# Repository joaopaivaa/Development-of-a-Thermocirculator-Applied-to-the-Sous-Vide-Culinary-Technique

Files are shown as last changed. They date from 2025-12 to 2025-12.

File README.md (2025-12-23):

## Development of a Thermocirculator Applied to the Sous Vide Culinary Technique

Paper in english published on "Revista Cereus" from Brazil (https://www.ojs.unirg.edu.br/index.php/1/article/view/5994)

Developed in 2019-2023 in collaboration with Erinaldo Nascimento, MSc and Camila Miranda, PhD as part of my electrical engineering BSc final paper and undergraduate research.

Abstract:
This paper addresses the theory, design, and execution of a thermocirculator, developing its electronic circuits, printed circuit boards (PCBs), plastic structure, and equipment assembling. The developed thermocirculator is based on 3 previous prototypes, with the first one being created in 2019. The ESP32 microcontroller was used as the basis for the electronic circuits. MicroPython was chosen as the programming language, and a web server was developed to connect the user and the equipment via Wi-Fi, allowing monitoring of the equipment from anywhere. An On-Off controller was implemented to keep the water temperature constant. The plastic structure was made of ABS plastic, and manufactured by 3D printing, with lateral dimensions of 7 x 7 cm and 18.5 cm of height, divided into upper portion, medial cover, lower portion, and lower covers. After the equipment was assembled, tests were made to verify its operation, which consisted of preparing foods such as a NY strip steak at 55 ºC, pork ribs at 70 ºC, and eggs at different temperatures. The developed thermocirculator performs its function excellently and can prepare food like a commercial product, fulfilling the objectives established by this paper.

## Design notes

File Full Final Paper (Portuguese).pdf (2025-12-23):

UNIVERSIDADE ESTADUAL DE MARINGÁ

DEPARTAMENTO DE ENGENHARIA QUÍMICA

CURSO DE ENGENHARIA ELÉTRICA

JOÃO VITOR DE PAIVA MARCOTTI

DESENVOLVIMENTO DE UM TERMOCIRCULADOR APLICADO À TÉCNICA CULINÁRIA SOUS VIDE

TRABALHO DE CONCLUSÃO DE CURSO

MARINGÁ

2023

JOÃO VITOR DE PAIVA MARCOTTI

DESENVOLVIMENTO DE UM TERMOCIRCULADOR APLICADO À TÉCNICA CULINÁRIA SOUS VIDE

Trabalho | de | Conclusão | de | Curso
apresentado | ao | Departamento | de
Engenharia Química, curso de Engenharia Elétrica da Universidade Estadual de
Maringá, | como | requisito | parcial à
obtenção | do | título de Engenheiro
Eletricista.

Orientador: Prof. Dr. Camila de Brito Miranda
Coorientador: Prof. Me. Erinaldo Sanches Nascimento

MARINGÁ

2023

- O Termo de Aprovação assinado encontra-se na Coordenação do Curso -

Dedico este trabalho à minha família e amigos, em especial à minha mãe, Patrícia Fernandes de Paiva, por todo o apoio e incentivo durante estes 5 anos de graduação.

AGRADECIMENTOS

Certamente estes parágrafos não irão atender a todas as pessoas que fizeram parte desta importante e única fase de minha vida, a graduação. Desta forma, devo citar os maiores responsáveis por todo o meu avanço ao longo destes 5 anos.
Primeiramente, agradeço à minha família por todo o incentivo aos estudos e apoio durante os bons e maus momentos deste período.
Agradeço à minha namorada por todo o apoio ao longo da realização deste trabalho, sendo, sem dúvidas, meu maior suporte emocional nos momentos de incerteza e insegurança.
Sou grato à minha orientadora Profa. Dra. Camila de Brito Miranda Faia, por todo o tempo, auxílio, preocupação e dedicação durante o desenvolvimento deste projeto.
Agradeço ao meu co-orientador Prof. Me. Erinaldo Sanches Nascimento, por toda a sua parceria e dedicação a este projeto que se iniciou como uma iniciação científica e se estendeu a este trabalho.
Aos meus colegas de vida e de sala de aula Felipe Gerber, Gabriel Dias, Gabriel Scapim e Kenzo Kayzuka, agradeço por toda a parceria durante os estudos, trabalhos e provas da faculdade, em especial durante a pandemia de Covid-19. Sempre juntos e apoiando uns aos outros nos bons e maus momentos. Sem vocês nada disso seria possível.
Devo mencionar também meu maior ídolo na gastronomia e por meio de quem conheci a técnica culinária Sous Vide, tema deste trabalho, Gustavo Tosta, mais conhecido como Guga Foods.
Agradeço meu pai, por todo o incentivo aos estudos e ao trabalho. Agradeço individualmente minha irmã, com quem divido a mesma moradia há 6 anos, e me apoia em minhas escolhas desde o ensino médio.
Por fim, enfatizo um agradecimento especial a quem me deu a vida e foi a única pessoa que nunca duvidou de mim, da minha capacidade, das minhas ideias e dos meus objetivos, e sempre foi o meu maior apoio, minha mãe Patricia Fernandes de Paiva.

Ideias, e somente ideias, podem iluminar a escuridão. (VON MISES, Ludwig)

RESUMO

MARCOTTI, João Vitor de Paiva. Desenvolvimento de um termocirculador aplicado à técnica culinária Sous Vide. 2023. 46 f. Trabalho de Conclusão de Curso (Bacharelado em Engenharia Elétrica) - Universidade Estadual de Maringá. Maringá, 2023.

Este trabalho aborda a teoria, o projeto e a execução de um termocirculador aplicado à técnica culinária Sous Vide, desenvolvendo seus circuitos eletrônicos, placas de circuito impresso (na sigla em inglês PCB - Printed Circuit Board), estrutura plástica, e até mesmo o planejamento de uma empresa fictícia responsável por desenvolver, fabricar, vender e distribuir termocirculadores. O termocirculador desenvolvido parte de 3 protótipos anteriores, sendo o primeiro elaborado em meados de 2019. O último, elaborado por Marcotti e Nascimento (2021), teve seu funcionamento impossibilitado em razão da grande quantidade de cabos conectores presentes em seu interior, o que impediu sua montagem. Desta forma, este projeto possui entre seus objetivos, a solução desta falha com a redução do número de cabos conectores, permitindo o funcionamento do equipamento. Como base para os circuitos eletrônicos desenvolvidos, utilizou-se o microcontrolador ESP32, que permite conexão Wi-Fi e Bluetooth entre usuário e equipamento. Para programar tal componente, utilizou-se a linguagem de programação MicroPython, e um servidor web foi desenvolvido a fim de conectar usuário e equipamento via Wi-Fi, permitindo o monitoramento deste de qualquer local com conexão à internet. Um controlador On-Off foi implementado com o objetivo de manter a temperatura da água constante durante o funcionamento do termocirculador. A estrutura plástica foi elaborada em plástico ABS, e fabricada via impressão 3D, possuindo como dimensões laterais 7 x 7 cm e altura de 18,5 cm, e é dividida em parte superior, tampa medial, parte inferior e tampas inferiores. Ainda, ímãs de neodímio localizados entre as tampas inferiores permitem que o termocirculador se fixe a um recipiente metálico. Após a montagem do equipamento, testes foram realizados com o objetivo de averiguar o funcionamento do termocirculador desenvolvido. Tais testes consistiram no preparo de alimentos, sendo eles bife de chorizo bovino a 55 ºC, costelinha suína a 70 ºC e ovos a diferentes temperaturas. A empresa fictícia foi nomeada como Termo 3D, em referência à fabricação da estrutura do equipamento, e seu planejamento foi elaborado contendo plano de negócios, modelo de negócios, marca e conclusão a respeito da viabilidade do negócio. A realização deste trabalho possibilitou colocar em prática diversos conhecimentos adquiridos em sala de aula, tais como o projeto de circuitos eletrônicos e de PCBs, além da análise e interpretação de datasheets de componentes. Por fim, pode-se afirmar que o termocirculador desenvolvido cumpre sua função com excelência, sendo capaz de preparar alimentos como um termocirculador comercializado no mercado, cumprindo os objetivos estabelecidos neste trabalho.

Palavras-chave: Controlador On-Off. Eletrônica. ESP32. Impressão 3D. MicroPython.

ABSTRACT

MARCOTTI, João Vitor de Paiva. Development of a thermocirculator applied to the Sous Vide culinary technique. 2023. 46 f. Trabalho de Conclusão de Curso (Bacharelado em Engenharia Elétrica) – Maringá State University - Paraná. Maringá, 2023.

This paper addresses the theory, design, and execution of a thermocirculator applied to the Sous Vide cooking technique, developing its electronic circuits, printed circuit boards (PCBs), plastic structure, and even the planning of a fictional company responsible for developing, manufacturing, selling, and distributing thermocirculators. The developed thermocirculator is based on 3 previous prototypes, with the first one being created in mid-2019. The last one, developed by Marcotti and Nascimento (2021), had its operation made impossible due to the large number of connector cables present inside, which prevented its assembly. Thus, one of the objectives of this project is to solve this flaw by reducing the number of connector cables, allowing the equipment to function. The ESP32 microcontroller was used as the basis for the developed electronic circuits, which allows Wi-Fi and Bluetooth connection between the user and the equipment. MicroPython programming language was used to program this component, and a web server was developed to connect the user and the equipment via Wi-Fi, allowing the monitoring of the equipment from anywhere with a connection. An On-Off controller was implemented to maintain the water temperature constant during the operation of the thermocirculator. The plastic structure was made of ABS plastic, and manufactured via 3D printing, with lateral dimensions of 7 x 7 cm and a height of 18.5 cm, divided into upper portion, medial cover, lower portion, and lower covers. Moreover, neodymium magnets located between the lower covers allow the thermocirculator to be fixed to a metallic container. After the equipment was assembled, tests were carried out to verify the operation of the developed thermocirculator, which consisted of preparing food such as NY strip steak at 55 ºC, pork ribs at 70 ºC, and eggs at different temperatures. The fictional company was named Termo 3D, referring to the manufacturing of the equipment's structure, and its planning included a business plan, a business model, a brand, and a conclusion regarding the business's viability. The accomplishment of this work made it possible to put into practice various knowledge acquired in the classroom, such as the design of electronic circuits and PCBs, as well as the analysis and interpretation of component datasheets. Finally, it can be said that the developed thermocirculator performs its function excellently, capable of preparing food like a thermocirculator marketed in the market, fulfilling the objectives established in this paper.

Keywords: 3D printing. Electronics. ESP32. Micropython. On-Off Controller.

LISTA DE ILUSTRAÇÕES

Figura 1 - Aplicação da técnica culinária Sous Vide. | 1
Figura 2 - Cocção por meio da técnica culinária Sous Vide. | 2
Figura 3 - Cocção por meio de técnica culinária tradicional (grelha à alta
temperatura). | 2
Figura 4 - Water oven Cetro Constantine. | 5
Figura 5 - Termocirculador Cetro SV95. | 6
Figura 6 - Microcontrolador ESP32-WROOM-32. | 8
Figura 7 - Conexões com o microcontrolador ESP32. | 13
Figura 8 - Ponte USB para UART. | 14
Figura 9 - Conexão do microcontrolador com um buzzer ativo. | 14
Figura 10 - Conexão entre microcontrolador e circuito de controle em tensão
alternada. | 15
Figura 11 - Conexão entre microcontrolador e display OLED. | 15
Figura 12 - Circuito divisor de tensão para coleta da variação de resistência de
um termistor. | 15
Figura 13 - LED indicador de alimentação. | 16
Figura 14 - Circuitos de pull up conectados ao microcontrolador. | 16
Figura 15 - Circuito de controle do motor CC (esquerda) e circuito de controle da
ventoinha (direita). | 17

Figura 16 - Conexão do microcontrolador com o sensor de nível d’água
(esquerda) e com o sensor de temperatura em sonda (direita). | 17
Figura 17 - Esquemático do circuito de alimentação. | 18
Figura 18 - Conversor AC-DC utilizado. | 18
Figura 19 - Regulador de tensão fixo LM1117-3.3. | 18
Figura 20 - Esquemático do circuito de controle em tensão alternada. | 19
Figura 21 - Placa de controle e alimentação. | 20
Figura 22 - Placa principal. | 20

Figura 23 - Disposição em torre das duas placas no interior do termocirculador. | 21
Figura 24 - Parte superior em vista isométrica. | 22
Figura 25 - Tampa medial em vista isométrica. | 23
Figura 26 - Parte inferior em vista isométrica. | 23
Figura 27 - Tampa inferior em vista isométrica. | 24
Figura 28 - Tampa inferior (imãs) em vista isométrica. | 24
Figura 29 - Vista isométrica da estrutura completa do termocirculador. | 25
Figura 30 - Fluxograma 1: Funcionamento da Etapa de Conexão Wi-Fi. | 30
Figura 31 - Fluxograma 2: Funcionamento do modo de espera do algoritmo de
programação desenvolvido. | 31

Figura 32 - Fluxograma 3: Funcionamento do modo de alerta do algoritmo de
programação desenvolvido. | 32

Figura 33 - Fluxograma 4: Funcionamento da primeira etapa do modo de
operação do algoritmo de programação desenvolvido. | 33

Figura 34 - Fluxograma 5: Funcionamento da segunda etapa do modo de
operação do algoritmo de programação desenvolvido. | 34

Figura 35 - Fluxograma 6: Funcionamento da terceira etapa do modo de
operação do algoritmo de programação desenvolvido. | 35

Figura 36 - Botão responsável por colocar o microcontrolador em modo de
download quando pressionado (KEY4). | 38

Figura 37 - Resistor (R1) e capacitor (C4) retirados da PCB após serem
destruídos em teste. | 39
Figura 38 - Página exibida pelo ponto de acesso para escolha da rede Wi-Fi. | 41
Figura 39 - Servidor web 1. | 42
Figura 40 - Servidor web 2. | 42
Figura 41 - Servidor web 3. | 42
Figura 42 - Modelo de Negócios Canvas elaborado. | 49
Figura 43 - Matriz SWOT. | 63
Figura 44 - Logo da empresa fictícia. | 64

Fotografia 1 - Periféricos presentes no termocirculador. | 11
Fotografia 2 - Faces da placa de controle e alimentação. | 25
Fotografia 3 - Faces da placa principal. | 26
Fotografia 4 - Foto da parte superior. | 26
Fotografia 5 - Foto da hélice. | 26
Fotografia 6 - Foto da parte inferior. | 27
Fotografia 7 - Foto da tampa medial. | 27
Fotografia 8 - Foto das duas partes da tampa de baixo. | 27
Fotografia 9 - Parafusos e porcas utilizados na montagem do termocirculador. | 28
Fotografia 10 - Termocirculador montado e completo. | 28
Fotografia 11 - Marca de incineração deixada na placa de controle e
alimentação. | 39
Fotografia 12 - Medição da diferença de potencial entre a panela e a bancada. | 40
Fotografia 13 - Medição da diferença de potencial entre a panela e a bancada
após a adição do fio de terra. | 40
Fotografia 14 - Termocirculador com temperatura desejada de 60 ºC. | 43
Fotografia 15 - Bife de chorizo preparado ao ponto menos (55 ºC). | 44
Fotografia 16 - Ovos cozidos a diferentes temperaturas (com casca). | 44

Fotografia 17 - Ovos cozidos a diferentes temperaturas (prontos para consumo). 45

Fotografia 18 - Costelinha suína preparada durante 4 horas. | 46
Gráfico 1 - Variação da temperatura da água pelo tempo. | 36
Gráfico 2 - Zoom da variação da temperatura da água pelo tempo. | 36
Gráfico 3 - Resistência do termistor em função da temperatura ambiente. | 37
Gráfico 4 - Taxa de sobrevivência de empresas em 2 anos de operação de
acordo com seu ano de fundação. | 48
Gráfico 5 - Faixa etária. | 52
Gráfico 6 - Renda em milhares de dólares. | 52

Gráfico 7 - Continente de residência. | 53
Gráfico 8 - Alimento mais preparado com o equipamento. | 53
Gráfico 9 - Maior atrativo para a compra do equipamento. | 53
Gráfico 10 - Valor máximo que pagaria em um termocirculador. | 54
Gráfico 11 - Fabricante de termocirculadores de preferência. | 54
Gráfico 12 - Se considera importante a presença de conexão wireless no
equipamento. | 54

Gráfico 13 - Se considera importante a disponibilidade de uma rede de
compartilhamento de receitas entre usuários. | 55
Gráfico 14 - Uso profissional ou amador do equipamento. | 55
Gráfico 15 - Composição do valor final de venda. | 60

LISTA DE QUADROS

Quadro 1 - Características dos materiais mais utilizados para impressão 3D. 9 Quadro 2 - Comparativo do termocirculador desenvolvido com pares de
mercado. | 47
Quadro 3 - Custos de fabricação dos circuitos eletrônicos por termocirculador. | 58
Quadro 4 - Custos de fabricação da estrutura plástica por termocirculador. | 59
Quadro 5 - Investimento fixo. | 61
Quadro 6 - Investimento em capital de giro inicial. | 61
Quadro 7 - Divisão do investimento inicial total. | 62

LISTA DE ABREVIATURAS, SIGLAS E ACRÔNIMOS

LISTA DE SIGLAS

ABS | Acrylonitrile Butadiene Styrene
AC | Alternating Current
CC | Corrente Contínua
DC | Direct Current
I2C | Inter-Integrated Circuit
ICMS | Imposto sobre Circulação de Mercadorias e Serviços
IDE | Integrated Development Environment
IPI | Imposto sobre Produtos Industrializados
LED | Organic Light-Emitting Diode
OLED | Light-Emitting Diode
P | Proporcional
PCB | Printed Circuit Board
PD | Proporcional Derivativo
P&D | Pesquisa e Desenvolvimento
PETG | Polyethylene Terephthalate Glycol
PI | Proporcional Integral
PID | Proporcional Integral Derivativo
PLA | Polylactic Acid
PTH | Pin Through Hole
SPI | Serial Peripheral Interface
SWOT | Strengths Weaknesses Opportunities Threats
UART | Universal Asynchronous Receiver/Transmitter

USB | Universal Serial Bus
TRIAC | Triode for Alternating Current
SCL | Serial Clock
SDA | Serial Data

LISTA DE ABREVIATURAS

Sebrae Serviço Brasileiro de Apoio às Micro e Pequenas Empresas

SUMÁRIO

1 INTRODUÇÃO | 1
2 FUNDAMENTAÇÃO TEÓRICA | 5
2.1 TERMOCIRCULADOR | 5
2.2 CONTROLADOR | 7
2.3 MICROCONTROLADOR | 8
2.4 IMPRESSÃO 3D | 9
3 METODOLOGIA | 11
4 DESENVOLVIMENTO | 13
4.1 PROJETO DOS CIRCUITOS ELETRÔNICOS | 13
4.1.1 Circuito Principal | 13
4.1.2 Circuito de Alimentação | 17
4.1.3 Circuito de Controle em Tensão Alternada | 18
4.1.4 Placas de De Circuito Impresso | 19
4.2 PROJETO DA ESTRUTURA PLÁSTICA | 22
4.3 EXECUÇÃO DAS PLACAS DE CIRCUITO IMPRESSO | 25
4.4 EXECUÇÃO DA ESTRUTURA PLÁSTICA | 26
4.5 ELABORAÇÃO DO ALGORITMO DE PROGRAMAÇÃO | 29
4.5.1 Por Que MicroPython? | 29
4.5.2 O Algoritmo | 29
4.6 IMPLEMENTAÇÃO DO CONTROLADOR ON-OFF | 35
4.7 FUNCIONAMENTO DO SENSOR DE TEMPERATURA INTERNA | 37
4.8 TESTES | 38
4.8.1 Teste dos Circuitos Eletrônicos | 38
4.8.2 Validação do Funcionamento do Algoritmo | 41
4.8.3 Bife de Chorizo Bovino | 43
4.8.4 Ovos | 44
4.8.5 Costelinha Suína | 45
4.9 COMPARATIVO DO TERMOCIRCULADOR DESENVOLVIDO COM PARES
DE MERCADO | 46
4.10 DESENVOLVIMENTO DE UMA EMPRESA FICTÍCIA | 47
4.10.1 Modelo de Negócio | 49
4.10.2 Plano de Negócios | 49
4.10.2.1 Sumário executivo | 50
4.10.2.1.1 O conceito do negócio | 50
4.10.2.1.2 O produto | 51
4.10.2.1.3 Equipe de gestão | 51
4.10.2.1.4 Missão | 51
4.10.2.2 Análise de mercado | 51
4.10.2.2.1 Cliente | 51

4.10.2.2.2 Concorrentes | 56
4.10.2.2.3 Fornecedores | 57
4.10.2.3 Plano de marketing | 57
4.10.2.3.1 Preço | 58
4.10.2.4 Plano operacional | 60
4.10.2.5 Plano financeiro | 61
4.10.2.5.1 Estimativa dos investimentos fixos | 61
4.10.2.5.2 Capital de giro | 61
4.10.2.5.3 Investimentos pré-operacionais | 62
4.10.2.5.4 Investimento total | 62
4.10.2.6 Avaliação estratégica | 62
4.10.2.6.1 Análise SWOT | 62
4.10.3 A Marca | 63
4.10.4 Conclusão Sobre a Viabilidade do Negócio | 64
5 CONCLUSÃO | 65
REFERÊNCIAS | 66

### 1 INTRODUÇÃO

Segundo Baldwin (2012), a palavra Sous Vide tem origem francesa, sendo traduzida para o português como “sob vácuo”. Já a técnica culinária Sous Vide, ilustrada na Figura 1, consiste na cocção de um alimento embalado a vácuo em um saco plástico e atóxico quando aquecido, e disposto em um recipiente contendo água a uma temperatura baixa e controlada (BORGES, 2019). Esta técnica culinária foi aplicada pela primeira vez em 1970 pelo chef do restaurante Troisgros, George Pralus, que buscava um método para preparar foie gras (traduzido do francês: fígado de pato) sem perder a consistência original do alimento (RAMOS, 2004).

Figura 1 - Aplicação da técnica culinária Sous Vide.

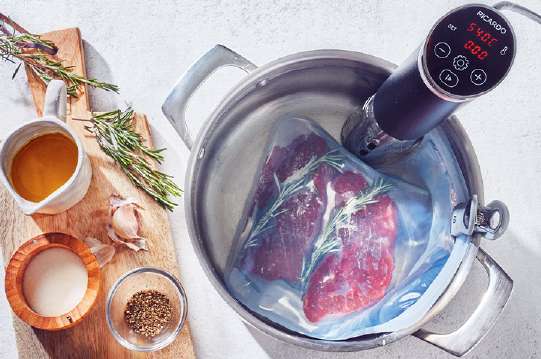
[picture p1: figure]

Fonte: Ricardo Cuisine (2022).

O fato do alimento estar embalado à vácuo permite que a transferência de calor entre água e alimento ocorra de forma mais eficiente, além de evitar a diluição de seus sabores na água (BORGES, 2019).
Segundo Ramos (2004), o sabor original dos alimentos, seus nutrientes e seus sucos naturais são preservados com o uso da técnica Sous Vide, o que resulta em uma qualidade e padronização de cocção impossíveis de se alcançar com o uso de métodos de preparo tradicionais. Além disso, esta técnica é capaz de eliminar todos os problemas de cor, sabor e textura dos alimentos, geralmente associados à comida congelada. Tem-se também, que a sua aplicação elimina os riscos de contaminação bacteriana dos alimentos, uma vez que durante o processo de cocção estes são totalmente pasteurizados e isolados do ambiente externo por meio da sua embalagem a vácuo.

Atualmente, o que mais chama a atenção do público e dos cozinheiros profissionais quanto ao uso da técnica culinária Sous Vide é, sem dúvida, a sua precisão quanto ao ponto de cocção do alimento, que, independente da sua espessura, sempre será fiel ao estabelecido pelo cozinheiro (CREED; REEVE, 1998). Ainda, os alimentos preparados por meio desta técnica mantém as suas propriedades organolépticas e nutricionais, além de se tornarem muito mais macios e saborosos do que quando preparados com o uso de técnicas convencionais (BALDWIN, 2012).
Desta forma, o uso da técnica Sous Vide, em razão da precisão e estabilidade da temperatura da água, resulta em uma cocção por igual em toda a extensão do alimento (Figura 2). Em comparação, quando se utiliza técnicas tradicionais no preparo de cortes de carnes, por exemplo o preparo em grelha a temperaturas elevadas, obtém-se como resultado um alimento com cocção excessiva em suas bordas e insuficiente em seu centro (Figura 3) (BORGES, 2019).

Figura 2 - Cocção por meio da técnica culinária Sous Vide.

Fonte: Borges (2019).

Figura 3 - Cocção por meio de técnica culinária tradicional (grelha à alta temperatura).

Fonte: Borges (2019).

Segundo Borges (2019), a técnica Sous Vide é composta por 4 etapas, sendo elas: tempero, embalagem, cocção e finalização.
Quanto à primeira etapa, tem-se que esta técnica culinária apresenta um efeito multiplicador do sabor de temperos e condimentos e, desta forma, deve-se tomar muito cuidado com as quantidades utilizadas (BORGES, 2019). Após isso, deve-se inserir o alimento em uma embalagem especial, atóxica e resistente à temperaturas elevadas, selando-a a vácuo por meio de uma seladora a vácuo. No entanto, o uso desta máquina pode ser substituído por outro processo, com resultado semelhante porém menos eficiente, que consiste em mergulhar a embalagem contendo o alimento em um recipiente com água e selá-lo quando houver vácuo em seu interior (BORGES, 2019).
Com o alimento temperado e embalado, tem-se a sua inserção em um recipiente com água à temperatura controlada e de acordo com o alimento ou receita a ser preparado. Assim como a temperatura, o tempo de cocção varia de acordo com a receita e alimento preparado, sendo recomendada 1 hora e meia por polegada de espessura de carnes vermelhas, por exemplo (BORGES, 2019). Durante a cocção do alimento por meio da técnica culinária Sous Vide, não há ocorrência de reação de Maillard em seu exterior, que consiste em uma reação química entre um aminoácido ou proteína e um carboidrato redutor, obtendo-se produtos que dão sabor, odor e cor aos alimentos, sendo o seu aspecto dourado após assados resultado desta reação (FRANCISQUINI et al., 2017). Desta forma, faz-se necessário à produzir por meio de um maçarico, frigideira ou grelha de forma rápida para preservar o ponto perfeito no interior do alimento. Esta é uma etapa que visa, principalmente, embelezar o alimento (BORGES, 2019).
Um termocirculador foi objeto de desejo do autor por muito tempo, porém adquirir um não se demonstrava racional diante dos elevados preços praticados pelos fabricantes deste tipo de equipamento. Desta forma, aliando tal desejo aos aprendizados obtidos durante a faculdade de engenharia elétrica, decidiu-se desenvolver o próprio termocirculador. Assim, este trabalho se trata do projeto da estrutura e dos circuitos eletrônicos de um termocirculador aplicado à técnica culinária Sous Vide, bem como da elaboração de um algoritmo de programação em MicroPython, e da implementação de um controlador On-Off para o controle da temperatura da água, culminando em um termocirculador de custo inferior ao praticado por seus pares de mercado. Além disso, este projeto engloba também o planejamento de uma empresa fictícia responsável pelo desenvolvimento, fabricação, comercialização e distribuição do equipamento desenvolvido. Este trabalho é baseado no protótipo projetado e executado por Marcotti e Nascimento (2021) e, desta forma, foi desenvolvido de forma a reparar falhas observadas e pontuadas pelos autores, como a grande quantidade de cabos conectores que impediu a montagem do equipamento, e adicionar melhorias.
Como objetivos específicos deste trabalho, tem-se o desenvolvimento dos circuitos eletrônicos e da estrutura do termocirculador; a elaboração de um algoritmo de programação para o microcontrolador em MicroPython, contando com a implementação de um controlador On-Off para o controle da temperatura da água; o planejamento de uma empresa fictícia responsável por seu desenvolvimento, fabricação, comercialização e distribuição e, por fim, a execução e teste de funcionamento do equipamento desenvolvido.

### 2 FUNDAMENTAÇÃO TEÓRICA

2.1 | TERMOCIRCULADOR
| Ao se utilizar da técnica culinária Sous Vide no preparo de alimentos, o
controle da temperatura da água pode ser feito de forma manual, substituindo a água do recipiente à medida que esfria, ou automática, utilizando-se um termocirculador ou um water oven que, por meio de sensores de temperatura, microcontrolador, aquecedor e outros componentes eletrônicos, são capazes de homogeneizar e manter a temperatura da água constante do início ao fim do preparo de um alimento.
| Segundo Borges (2019), water oven (Figura 4) se trata de um equipamento
que possui todas as funções necessárias para a prática da técnica culinária Sous Vide, dispensando objetos adicionais. Possui como vantagem, um compartimento que reserva e aquece água. Seu elemento aquecedor tipicamente se localiza no fundo da unidade, sendo estrategicamente posicionado de forma a aproveitar que a água se torna menos densa à medida que esquenta e proporcionar um aquecimento mais uniforme.

Figura 4 - Water oven Cetro Constantine.

Fonte: Cetro Máquinas (2022a).

Já um termocirculador (Figura 5) necessita de um recipiente contendo água, ao qual é devidamente fixado, para possibilitar o seu funcionamento. O recipiente deve possuir dimensões de forma que o equipamento não fique submerso mas também não fique excessivamente fora da água. Ainda, um motor com hélice, ou uma bomba, é responsável pela circulação da água, visto que apenas seu aquecedor não possibilita uma temperatura uniforme em todo o recipiente. Atualmente, alguns termocirculadores já possuem módulos Wi-Fi ou Bluetooth, permitindo controle e monitoramento remotos do equipamento (BORGES, 2019).

Figura 5 - Termocirculador Cetro SV95.

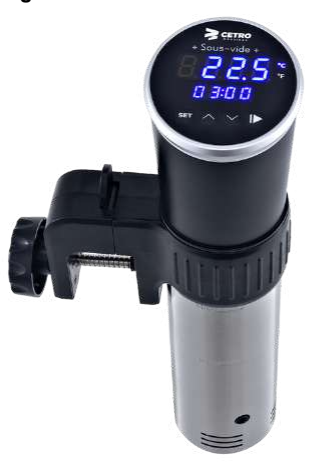
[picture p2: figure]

Fonte: Cetro Máquinas (2022b).

Segundo Borges (2019), se comparado ao water oven, o termocirculador se trata de um equipamento mais econômico e compacto, podendo ser facilmente transportado e armazenado, ideal para cozinhas pequenas e amadoras.
Chefsteps Joule e Anova Precision Cooker são os termocirculadores de maior destaque no mercado mundial. Ambos os equipamentos possuem conexão Wi-Fi ou Bluetooth com smartphones, permitindo controlá-los remotamente. Apresentam diversas funcionalidades, sendo a principal o envio de informação para/do termocirculador. Além disso, páginas de ajuda, notificações do estado do equipamento, comunidades de receitas e tutoriais em vídeo também podem ser encontrados nos aplicativos mobile dos equipamentos mencionados (BORGES, 2019).
Quanto ao mercado brasileiro, a empresa de maior destaque se trata da Cetro Máquinas, contendo em seu catálogo de produtos tanto termocirculadores quanto water ovens.

2.2 | CONTROLADOR
| Diversos controladores podem ser implementados para a manutenção da
temperatura da água, tais como controlador On-Off, P (Proporcional), PI (Proporcional e Integral), PD (Proporcional e Derivativo) ou PID (Proporcional, Integral e Derivativo).
| Segundo Silva (2018), em muitos processos com constantes de tempo
simples, é comum usar o controlador P, que é sensível a perturbações e mudanças no ponto de ajuste. No entanto, essa abordagem geralmente leva a um erro residual em regime permanente (offset), o que é considerado indesejável.
| O controle integral tem como principal característica a redução ou eliminação
do erro em regime permanente. No entanto, se o ganho integral for muito alto ou a resolução do sensor for baixa, a resposta pode se tornar excessivamente oscilatória, o que é uma desvantagem. Para contornar essa limitação, é comum adicionar ganho proporcional e, se necessário, atenuar o ganho integral (SILVA, 2018)
| Por sua vez, o controlador PD adiciona um zero na função de transferência do
sistema, melhorando o desempenho em regime transitório e aumentando a estabilidade relativa do sistema, o que reduz o tempo de acomodação. No entanto, embora tenha essas vantagens, o controlador derivativo aumenta o tempo de subida e não corrige o erro de estado estacionário, já que não atua nesse regime (SILVA, 2018).
| O controlador PID une os controladores proporcional, integral e derivativo,
atuando tanto no regime transitório quanto no regime permanente, combinando as características de estabilidade de controle proporcional derivativo com as características de eliminação do erro oferecidas pelo controle proporcional integral. Além disso, este controlador reduz o erro em regime permanente e melhora a estabilidade do sistema controlado, no entanto, a resposta do sistema pode ser lenta quando comparada a outros controladores (SILVA, 2018) (FERRANDO; ARAUJO; KAKUNO, 2017).
| O controlador On-Off pertence ao grupo de controle clássico, e funciona
baseado na leitura de um sensor (neste caso, de temperatura da água), que atua no sistema de modo a atingir um objetivo em específico (neste caso, a manutenção de temperatura da água) ligando e desligando um atuador (neste caso, um ebulidor)

(CARDOSO, 2020). Para este trabalho, optou-se pelo uso do controlador On-Off, que será justificado adiante.

2.3 | MICROCONTROLADOR
| Como referência para o projeto de todos os circuitos eletrônicos deste
trabalho, optou-se pelo uso do microcontrolador ESP32 (Figura 6). Trata-se de um componente fabricado pela empresa Espressif Systems, apresenta conexão Wi-Fi, com frequência de 2,4 GHz, e Bluetooth, possibilitando diversas aplicações. Este microcontrolador possui um cristal oscilador integrado de 40 MHz em seu interior, dispensando o uso de um componente externo. Sua tensão de alimentação pode variar entre 3 e 3,6 V, com uma corrente de operação média de 80 mA, e pode trabalhar em temperaturas entre -40 °C e +85 °C. Ainda, trata-se de um componente compacto, dispondo de dimensões iguais a 18 x 25,50 x 3,10 mm. Apresenta comunicação por meio dos padrões I2C e SPI. Somando todas as suas portas digitais, o ESP32 é capaz de entregar uma corrente de saída de até 1,1 A. (ESPRESSIF SYSTEMS, 2021).

Figura 6 - Microcontrolador ESP32-WROOM-32.

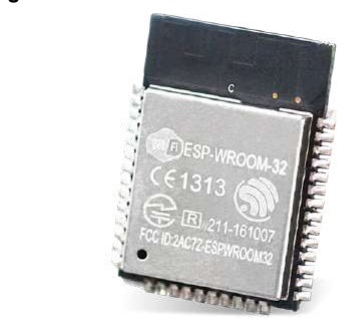
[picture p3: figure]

Fonte: Mouser Electronics (2018).

Para a programação do microcontrolador ESP32, foi utilizada a linguagem de programação de alto nível MicroPython, derivada de Python 3, que inclui diversas subfunções de bibliotecas padrão Python, porém otimizadas para trabalhar com microcontroladores. Desta forma, assim como Python se faz em relação a C/C++, a linguagem de programação MicroPython se mostra mais simples e intuitiva do que a presente no ambiente de programação Arduino IDE, além de tornar o protótipo desenvolvido mais profissional (TEIXEIRA, 2019).

2.4 | IMPRESSÃO 3D
| Normalmente, quando se trata de impressão 3D, três materiais se destacam:
o Acrilonitrila Butadieno Estireno (na sigla em inglês ABS: Acrylonitrile Butadiene Styrene), o Ácido Polilático (na sigla em inglês PLA: Polylactic Acid) e o Polietileno Tereftalato Glicol (na sigla em inglês PETG: Polyethylene Terephthalate Glycol). Suas principais características estão exibidas no Quadro 1.

Quadro 1 - Características dos materiais mais utilizados para impressão 3D.
Propriedades | Material
PLA | ABS | PETG
Densidade | 1,24 g/cm3 | 1,04 g/cm3 | 1,27 g/cm3
Temperatura de fusão | 185 ºC | 220 ºC | 240 ºC
Temperatura de transição vítrea | 60 ºC | 100 ºC | 85 ºC
Tensão de escoamento | 66 Mpa | 38 Mpa | 51 Mpa
Resistência à flexão | 130 Mpa | 66 Mpa | 72 Mpa
Módulo de elasticidade | 4350 Mpa | 2200 Mpa | 2120 Mpa
Valor por quilograma | R$ 98,01 | R$ 65,90 | R$ 107,01
Qualidade de acabamento | Baixa | Alta | Média

Fonte: Galvani (2019), 3D Lab (2023a), 3D Lab (2023b) e 3D Lab (2023c).

O ABS, material utilizado neste trabalho, trata-se do termoplástico mais antigo, barato e comum, sendo derivado do petróleo e, portanto, de origem não renovável. Segundo Galvani (2019), objetos feitos deste material são resistentes mecanicamente e levemente flexíveis, tornando-o ideal para a produção de peças que precisem suportar cargas mecânicas e impactos. Também são consideravelmente resistentes à umidade e a temperatura, com temperatura de fusão e transição vítrea iguais a 220 ºC e 100 ºC respectivamente. Por estas características, costumam ser escolhidos para protótipos industriais.
Por sua vez, o PLA é um material biodegradável e de origem vegetal, podendo ser feito de amido de milho, cana-de-açúcar, raízes de tapioca ou amido de batata. Segundo Galvani (2019), trata-se de um material mais sensível ao calor e que necessita ser guardado em lugares frescos e secos, caso contrário, torna-se quebradiço e pode apresentar problemas. Apresenta temperatura de fusão e transição vítrea iguais a 185 ºC e 60 ºC respectivamente.
Já o PETG, segundo Galvani (2019), é considerado um material nobre para a impressão 3D em razão de suas características de alta resistência mecânica e química. Apresenta resistência à temperatura próxima ao plástico ABS, com temperatura de fusão e transição vítrea iguais a 240 ºC e 85 ºC respectivamente.

### 3 METODOLOGIA

Inicialmente, realizou-se uma revisão de literatura, estudando tópicos a respeito da técnica culinária Sous Vide e aplicações do termocirculador a mesma,
bem | como | assuntos | relacionados | à | empreendedorismo, | eletrônica,
microcontroladores e linguagens de programação.
Posteriormente, projetou-se, por meio do software EasyEDA, os circuitos eletrônicos que compõem o equipamento desenvolvido, baseados no microcontrolador ESP32 e seu datasheet. Estes circuitos foram agrupados na forma de placas de circuito impresso (na sigla em inglês PCB - Printed Circuit Board), que foram encomendadas por meio da fabricante JLC PCBs.
Após isso, os periféricos que se comunicam com o microcontrolador, enviando informações ou sendo controlados por ele, foram escolhidos e adquiridos. São eles exibidos na Fotografia 1 da esquerda para a direita: ebulidor (aquecedor de água), sensor de nível de água, sensor de temperatura em sonda, motor de corrente contínua (CC) e ventoinha.

Fotografia 1 - Periféricos presentes no termocirculador.

Fonte: Autoria própria.

Com a definição dos periféricos e aquisição dos mesmos, foi desenvolvida a estrutura plástica do termocirculador por meio do software Autodesk Inventor, de forma a alocar todas as PCBs e periféricos com segurança. Em seguida, a mesma foi fabricada em plástico ABS com o uso de impressão 3D.
As placas de circuito impresso e periféricos foram alocados na estrutura do termocirculador e, com isso, por meio do ambiente de desenvolvimento Thonny, disponível em Thonny (2023), foi elaborado um algoritmo de programação na linguagem MicroPython de forma a controlar o microcontrolador escolhido (ESP32), o comunicar com o usuário do equipamento por meio de um servidor web via conexão Wi-Fi e implementar um controlador On-Off para estabilizar a temperatura da água controlada durante o período de funcionamento do equipamento.
Com a finalização do algoritmo de programação, planejou-se uma empresa fictícia para a comercialização do termocirculador desenvolvido neste trabalho, contendo nome, logo e todo o estudo, planejamento e projeções necessárias para a abertura de uma empresa real.
Por fim, iniciou-se a fase de testes do equipamento desenvolvido, contando com a preparação de alimentos por meio da técnica culinária Sous Vide, sendo eles bife de chorizo, costelinha suína e ovos.

### 4 DESENVOLVIMENTO

4.1 | PROJETO DOS CIRCUITOS ELETRÔNICOS
| Os circuitos eletrônicos do termocirculador desenvolvido foram divididos em
três: circuito principal, de alimentação e de controle em tensão alternada.

4.1.1 Circuito Principal

| O circuito principal é responsável pelo processamento de informações
coletadas pelos botões e sensores de nível e temperatura de água, controle do display OLED, motor CC e ventoinha e manutenção da conexão wireless com o usuário. Este circuito foi baseado no microcontrolador ESP32 e seu datasheet.
| A principal necessidade deste circuito é reduzir os cabos de conexão
presentes no interior do equipamento e que, segundo Marcotti e Nascimento (2021), dificultam a sua montagem.
| Na Figura 7, tem-se as conexões necessárias para o funcionamento
adequado do microcontrolador, obtidas a partir do datasheet do componente.

Figura 7 - Conexões com o microcontrolador ESP32.

Fonte: Autoria própria.

Quanto à programação do microcontrolador, foram necessários dois botões: um para atribuir sinal lógico baixo à sua porta digital 0, permitindo que o microcontrolador entre em modo boot, possibilitando o envio de firmwares e algoritmos para ele, e outro para atribuir sinal lógico baixo ao seu pino EN, resetando o estado do microcontrolador (este botão não constava no datasheet e no circuito de referência do componente, porém foi necessário). Além disso, as portas TXD0 e RXD0 permitem a sua comunicação com um computador por meio de uma ponte USB para UART com o controlador CP2102 (Figura 8).

Figura 8 - Ponte USB para UART.

Fonte: Daraz (2023).

Além disso, dois pólos positivos de 3,3 V e 5 V e um GND alimentam o microcontrolador, que pode ser alimentado com tensões entre 3 V e 3,6 V, e os demais componentes do circuito principal.
Sua porta digital 4 (IO4) se conecta a um resistor e um buzzer ativo, responsável por emitir um aviso sonoro para alertar o usuário do equipamento caso este seja ligado fora d’água, evitando graves acidentes (Figura 9).

Figura 9 - Conexão do microcontrolador com um buzzer ativo.

Fonte: Autoria própria.

O microcontrolador se conecta com o circuito de controle em tensão alternada por meio de sua porta digital 16 (IO16) e dois soquetes macho (placa principal) e dois soquetes fêmea (placa de controle e alimentação) (Figura 10).

Figura 10 - Conexão entre microcontrolador e circuito de controle em tensão alternada.

Fonte: Autoria própria.

Suas portas digitais 21 (IO21/SDA) e 22 (IO22/SCL) se conectam ao display OLED (Figura 11), permitindo a comunicação com este componente e possibilitando exibir mensagens de texto no mesmo.

Figura 11 - Conexão entre microcontrolador e display OLED.

Fonte: Autoria própria.

Para coletar valores de temperatura provenientes de um termistor NTC, por meio da variação de sua resistência, utilizou-se um circuito divisor de tensão conectado à sua porta digital 35 (IO35), que dispõe de conversor analógico-digital (Figura 12).

Figura 12 - Circuito divisor de tensão para coleta da variação de resistência de um termistor.

Fonte: Autoria própria.

Um LED verde conectado a um resistor é disposto entre os pólos de 3 V e GND, indicando se a placa principal está ou não sendo alimentada (Figura 13).

Figura 13 - LED indicador de alimentação.

Fonte: Autoria própria.

Um resistor de pull up é conectado à porta digital 34 (IO34), representando o botão de incremento de temperatura. Já a porta digital 18 (IO18) é conectada diretamente ao botão, pois possui suporte para resistores de pull-up ou pull-down internos via software, representando o botão de decremento de temperatura (Figura 14).

Figura 14 - Circuitos de pull up conectados ao microcontrolador.

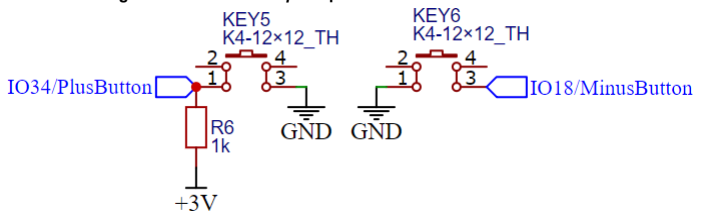
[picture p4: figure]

Fonte: Autoria própria.

O controle do motor CC e da ventoinha ocorre por meio de dois transistores NPN 2SC1815, com estes ligados às portas digitais 26 (IO26) e 25 (IO25) do microcontrolador, respectivamente (Figura 15).
Deve-se pontuar que a ausência de resistores entre as portas digitais e a base dos transistores se deu por uma falha de projeto, podendo ocasionar a saturação do transistor e o consequente aumento da dissipação de energia, danificando o mesmo e impedindo seu funcionamento. Portanto, é necessária a adição desses resistores (BOYLESTAD; NASHELSKY, 2013).

Figura 15 - Circuito de controle do motor CC (esquerda) e circuito de controle da ventoinha (direita).

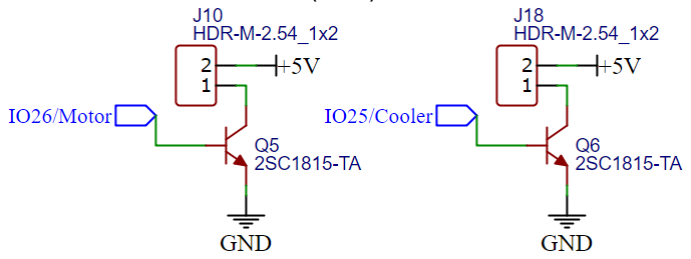
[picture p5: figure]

Fonte: Autoria própria.

Já o sensor de nível d’água e o sensor de temperatura em sonda se conectam às portas digitais 32 (IO32/ADC1CH4) e 33 (IO33/ADC1CH5) respectivamente, com suporte aos conversor analógico-digital 1 e seus canais 4 e 5 e sendo alimentados pelo pólo de 3 V e GND. Além disso, o sensor de temperatura em sonda demanda um resistor de 4,7 kΩ em configuração de pull-up (Figura 16).

Figura 16 - Conexão do microcontrolador com o sensor de nível d’água (esquerda) e com o sensor de temperatura em sonda (direita).

Fonte: Autoria própria.

4.1.2 Circuito de Alimentação

Como fonte de energia para o microcontrolador e demais componentes eletrônicos, foi utilizado um conversor 110 VAC - 5 VDC com potência de 10 W (Figura 18), adquirido por meio do marketplace Banggood. Este conversor é composto, basicamente, por transformador, ponte retificadora, capacitores e resistores. O circuito de alimentação completo está disposto na Figura 17.

Figura 17 - Esquemático do circuito de alimentação.

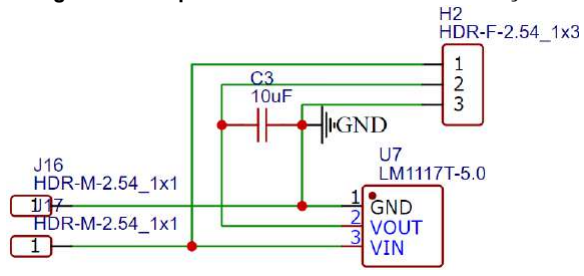
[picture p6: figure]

Fonte: Autoria própria.

Figura 18 - Conversor AC-DC utilizado.

Fonte: Joom (2023).

Com o intuito de rebaixar a tensão de 5V proveniente do conversor AC-DC para 3,3 V, utilizou-se o regulador de tensão fixo LM1117-3.3 (Figura 19), posicionado na saída do componente (J16 ligado ao GND e J17 ao pólo de 5 V).

Figura 19 - Regulador de tensão fixo LM1117-3.3.

Fonte: Aliexpress (2023).

4.1.3 Circuito de Controle em Tensão Alternada

Já o circuito de controle em tensão alternada (Figura 20), responsável pelo funcionamento adequado do ebulidor (equipamento responsável pelo aquecimento da água), foi baseado no trabalho de Borges (2019) e é composto, basicamente, por um TRIAC (BTB12) e um optoacoplador (MOC3023), este próprio para o acionamento de TRIACs conectados a tensão da rede elétrica (ON SEMICONDUCTOR, 2018).

O optoacoplador age como um isolador entre o microcontrolador e a tensão da rede elétrica e, ao receber o sinal lógico alto proveniente do microcontrolador, aciona o TRIAC. Desta forma, tem-se a passagem de corrente alternada pelo ebulidor, conectado à placa de controle e alimentação por meio de conectores do tipo borne (U8), aquecendo a água contida no recipiente no qual o termocirculador está posicionado.

Figura 20 - Esquemático do circuito de controle em tensão alternada.

Fonte: Autoria própria.

O conector borne U9 se conecta à tensão proveniente da rede elétrica doméstica por meio de uma tomada convencional, que também se conecta às entradas do conversor AC-DC.

4.1.4 Placas de De Circuito Impresso

Pensando na completa fabricação do equipamento, os 3 circuitos projetados foram agrupados e elaborados na forma de 2 placas de circuito impresso (Figuras 21 e 22), com designs pensados para diminuir ao máximo as dimensões do termocirculador e reduzir a quantidade de cabos de conexão em seu interior, facilitando a sua montagem.

Figura 21 - Placa de controle e alimentação.

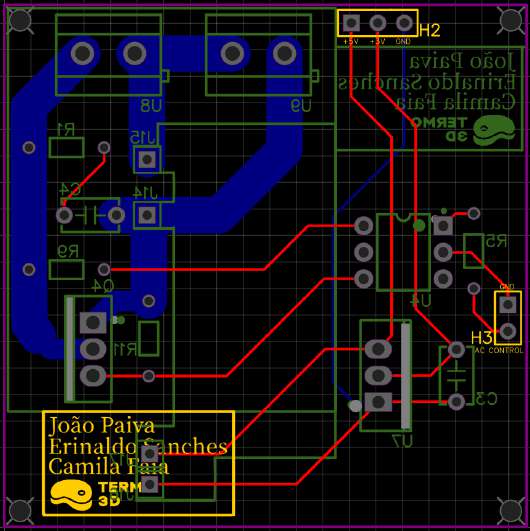
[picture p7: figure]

Fonte: Autoria própria.

Figura 22 - Placa principal.

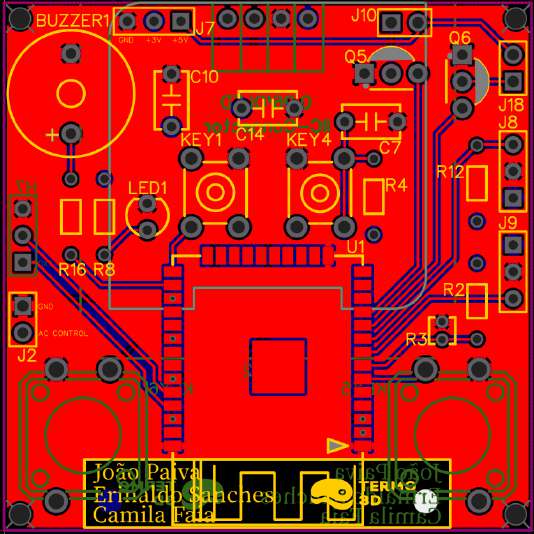
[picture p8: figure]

Fonte: Autoria própria.

Quanto à placa de controle e alimentação (Figura 21), deve-se destacar os cálculos relacionados à largura de suas trilhas conectadas ao ebulidor e, consequentemente, à tensão alternada, garantindo que uma determinada corrente possa ser conduzida sem causar superaquecimento ou danos à placa. Portanto, com base na norma técnica IPC-2221A (IPC, 2003), a Equação 1 descreve a largura da trilha (L), em milímetros, para um determinado aumento de temperatura (ΔT) quando percorrida por uma corrente (I), em que k é uma constante que varia de acordo com a localização da trilha, sendo igual a 0,048 para trilhas externas, e E se refere à espessura do cobre, sendo esta igual a 1 onças (oz), ou 28,4 g, para a fabricação padrão por meio da empresa JLC PCBs.

L = 0, 0254 | (1)

(

I
k.ΔT

0,44 )

1
0,725

1,378.E

Para este projeto, considerando trilhas externas, variação de temperatura (ΔT) igual a 10 ºC e corrente (I) igual a 6 A, tem-se a largura de trilha calculada igual a 3,5 milímetros.
As duas PCBs elaboradas possuem as mesmas dimensões laterais: 5 cm x 5 cm, permitindo o seu posicionamento em torre (uma em cima da outra) por meio de parafusos hexagonais de nylon, empregados a fim de reduzir a massa da região superior do termocirculador, conforme mostrado na Figura 23. Soquetes macho e fêmea foram utilizados para conectar as PCBs.

Figura 23 - Disposição em torre das duas placas no interior do termocirculador.

Fonte: Autoria própria.

4.2 | PROJETO DA ESTRUTURA PLÁSTICA
| A estrutura do termocirculador desenvolvido foi dividida em 4 partes, visando
facilitar a sua montagem e fabricação via impressão 3D: parte superior, parte inferior, tampa medial e tampas inferiores 1 e 2.
| A parte superior (Figura 24), foi projetada de forma a conter e proteger as 2
placas de circuito impresso dispostas em torre em seu interior, além de ventoinha, motor CC, display OLED e botões. Em sua face traseira, tem-se a presença de um orifício que possibilita a entrada dos fios de tensão alternada, em suas laterais há vãos que permitem a saída do ar quente, e em sua face frontal tem-se a logo da empresa fictícia responsável pela produção e comercialização deste equipamento, a Termo 3D. Dispõe de dimensões laterais iguais a 7 x 7 cm, e altura igual a 5,5 cm.

Figura 24 - Parte superior em vista isométrica.

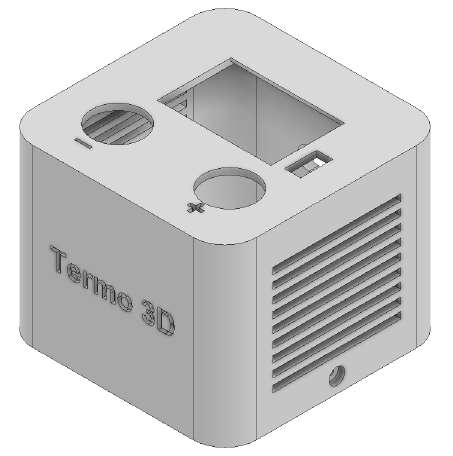
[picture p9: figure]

Fonte: Autoria própria.

Já a tampa medial (Figura 25), foi elaborada de forma a fixar o motor CC, a ventoinha e os parafusos hexagonais que mantém as 2 PCBs posicionadas em torre. Além disso, é responsável por ligar as porções superior e inferior do termocirculador. Dispõe de dimensões laterais iguais a 7 x 7 cm, e espessura igual a 3 mm.

Figura 25 - Tampa medial em vista isométrica.

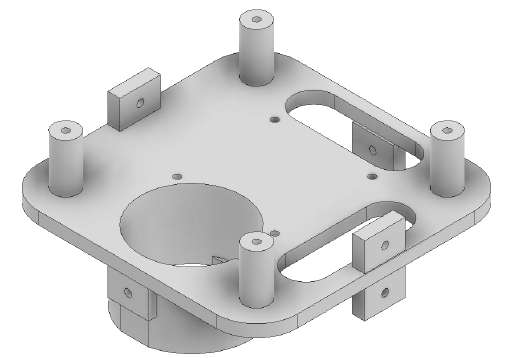
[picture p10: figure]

Fonte: Autoria própria.

A parte inferior do termocirculador (Figura 26) é a sua maior parte, e abriga o ebulidor, componente responsável por aquecer a água, o sensor de temperatura em sonda, o sensor de nível d’água e a hélice. Essa parte é mostrada na Figura 3, e possui dimensões laterais iguais a 7 x 7 cm, e altura igual a 12,5 cm.

Figura 26 - Parte inferior em vista isométrica.

Fonte: Autoria própria.

Por fim, tem-se a tampa inferior, que é composta por duas partes (Figuras 27 e 28), e contém em seu interior os ímãs de neodímio (de dimensões iguais a 16 x

16 x 2 mm) responsáveis pela fixação do termocirculador. Esta peça sela a parte inferior do equipamento, possuindo vãos que permitem a entrada de água em seu interior e possui as mesmas dimensões laterais iguais a 7 x 7 cm e espessura somada de 5 mm.

Figura 27 - Tampa inferior em vista isométrica.

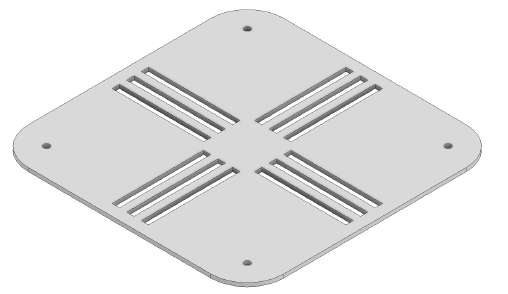
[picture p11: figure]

Fonte: Autoria própria.

Figura 28 - Tampa inferior (imãs) em vista isométrica.

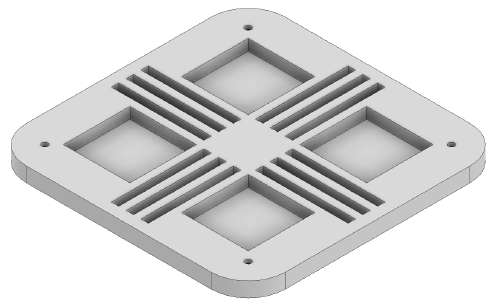
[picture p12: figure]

Fonte: Autoria própria.

Todas as partes que compõem o termocirculador, mencionadas anteriormente, foram pensadas e projetadas para serem fabricadas por meio de impressão 3D e compostas por plástico ABS. Optou-se pelo uso deste material em razão do mesmo possuir boa resistência mecânica, ponto de fusão superior à temperatura da água durante o funcionamento do equipamento (máximo de 80 ºC). Desta forma, com base no Quadro 1, considerou-se este material superior às outras opções disponíveis.
Portanto, tem-se que a estrutura do termocirculador desenvolvido dispõe de dimensões laterais iguais a 7 x 7 cm e altura total de 18,5 cm. A estrutura completa é apresentada na Figura 29.

Figura 29 - Vista isométrica da estrutura completa do termocirculador.

Fonte: Autoria própria.

4.3 | EXECUÇÃO DAS PLACAS DE CIRCUITO IMPRESSO
| As 2 placas de circuito impresso desenvolvidas (Fotografias 2 e 3) tiveram
seus arquivos .gerber exportados, foram encomendadas por meio da fabricante JLC PCBs e seus componentes eletrônicos foram soldados com o uso de ferro de solda convencional, utilizando-se componentes de montagem PTH (Pin Through Hole, com tradução do inglês: Pino Através de Orifício).

Fotografia 2 - Faces da placa de controle e alimentação.

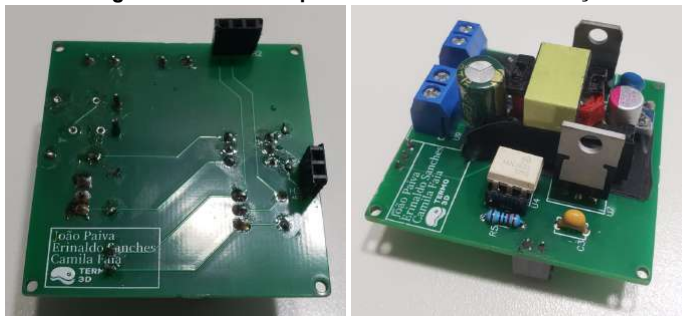
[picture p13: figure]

Fonte: Autoria própria.

Fotografia 3 - Faces da placa principal.

Fonte: Autoria própria.

4.4 | EXECUÇÃO DA ESTRUTURA PLÁSTICA
| Todas as partes que compõem a estrutura do termocirculador foram
confeccionadas via impressão 3D em plástico ABS de cor preta e cinza, e estão dispostas nas Fotografias 4 à 8.

Fotografia 4 - Foto da parte superior.

Fonte: Autoria própria.

Fotografia 5 - Foto da hélice.

Fonte: Autoria própria.

Fotografia 6 - Foto da parte inferior.

Fonte: Autoria própria.

Fotografia 7 - Foto da tampa medial.

Fonte: Autoria própria.

Fotografia 8 - Foto das duas partes da tampa de baixo.

Fonte: Autoria própria.

Para se fixar as partes fabricadas, utilizou-se 16 parafusos M2 convencionais e 4 de nylon, 2 porcas convencionais e 8 parafusos hexagonais de nylon (Figura 9).

Fotografia 9 - Parafusos e porcas utilizados na montagem do termocirculador.

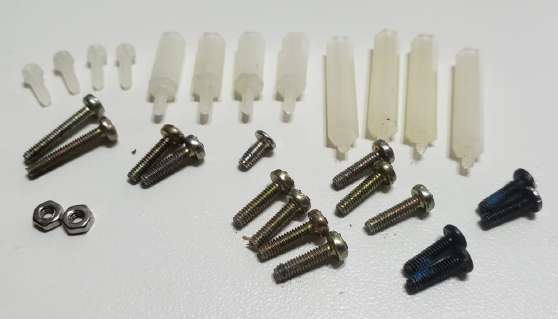
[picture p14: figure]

Fonte: Autoria própria.

Desta forma, com o equipamento montado e completo, assim como previsto durante a etapa de projeto, tem-se dimensões laterais iguais a 7 x 7 cm e altura igual a 18,5 cm, além de design em cor preta com detalhes cinzas (Fotografia 10).

Fotografia 10 - Termocirculador montado e completo.

Fonte: Autoria própria.

4.5 ELABORAÇÃO DO ALGORITMO DE PROGRAMAÇÃO

4.5.1 Por Que MicroPython?

| Optou-se pelo uso da linguagem de programação MicroPython em razão da
vasta quantidade de cursos e materiais disponíveis na internet e com fácil acesso relacionados à sua aplicação junto ao microcontrolador ESP32. Além disso, esta linguagem de programação despertava o interesse do autor e apresenta uma biblioteca específica para a implementação de um servidor web, nomeada como Wifimgr, facilitando uma importante etapa deste trabalho.
| Ainda, acredita-se que o uso desta linguagem de programação diferencia este
trabalho de outros relacionados a circuitos microcontrolados, uma vez que a mesma não é frequentemente empregada como C/C++, além de contribuir para a sua popularização.
| Por fim, assim como Python se faz em relação a C/C++, a linguagem de
programação MicroPython se mostra mais simples e intuitiva do que a presente no ambiente de programação Arduino IDE. Além disso, torna o protótipo desenvolvido por este projeto muito mais profissional (TEIXEIRA, 2019).

4.5.2 O Algoritmo

| O algoritmo de programação desenvolvido fez uso das bibliotecas Socket
(2023) e Wifimgr, disponível em Ulu (2023), para conexão Wi-Fi e gerenciamento do servidor web, Onewire (2023) e DS18X20 (2023) para controle do sensor de temperatura em sonda, SH1106, disponível em Hammelrath (2023), para controle do display OLED, Time (2023) para adição de estruturas de delay, Math (2023) para os cálculos necessários para a conversão da temperatura lida pelo termistor e Machine (2023) para o controle das portas digitais, conversores analógicos digitais e demais funções de hardware do microcontrolador.
| A estrutura de funcionamento do algoritmo desenvolvido segue os
fluxogramas apresentados nas Figuras 30 a 35.
| A Etapa de Conexão Wi-Fi (Figura 30) é o momento no qual o termocirculador
tenta se conectar à uma das redes Wi-Fi presentes em seu histórico de conexões. Caso não seja possível, ele habilita um ponto de acesso para que o usuário insira as informações sobre a rede a qual ele deve se conectar. Um endereço IP com destino à página web referente ao ponto de acesso é exibido no display do termocirculador, bem como o nome e a senha da rede Wi-Fi referente a ele. Caso não haja conexão à uma rede, o termocirculador aguarda para executar o restante do algoritmo. Ou seja, para funcionar, o equipamento necessita estar conectado à uma rede Wi-Fi, porém não exige que o servidor web seja mantido aberto em um dispositivo.

Figura 30 - Fluxograma 1: Funcionamento da Etapa de Conexão Wi-Fi.

Fonte: Autoria própria.

Já o Modo de Espera (Figura 31) é o momento no qual o equipamento exibe em seu display a representação de uma face dormindo, em alusão ao fato de estar esperando que o usuário posicione e o ative ao pressionar seus 2 botões físicos ou o botão presente no servidor web. Neste momento, também é exibido o endereço IP de acesso ao servidor web.

Figura 31 - Fluxograma 2: Funcionamento do modo de espera do algoritmo de programação desenvolvido.

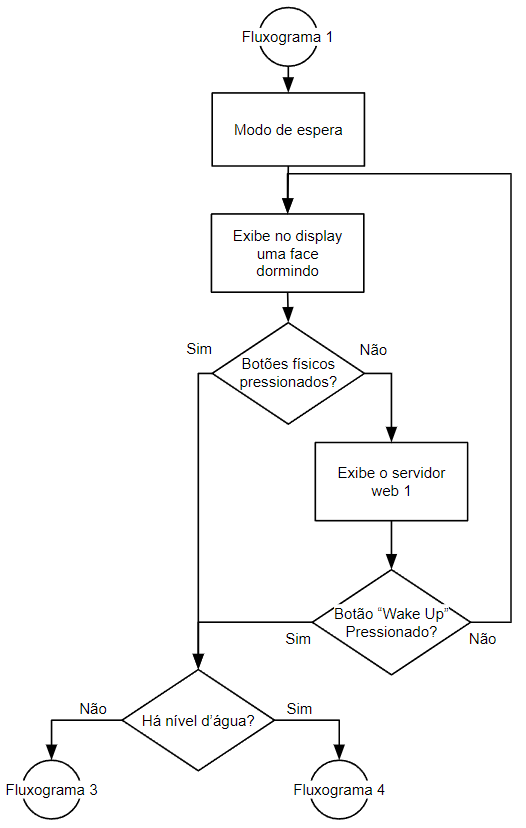
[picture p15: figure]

Fonte: Autoria própria.

O Modo de Alerta (Figura 32) ocorre quando o termocirculador é ativado fora d’água. Tendo em vista que o ebulidor pode vir a derreter nesta situação, e a fim de se evitar acidentes, uma mensagem de aviso é exibida no display, o buzzer é ativado como forma de alertar o usuário e o ebulidor é desligado.

Figura 32 - Fluxograma 3: Funcionamento do modo de alerta do algoritmo de programação desenvolvido.

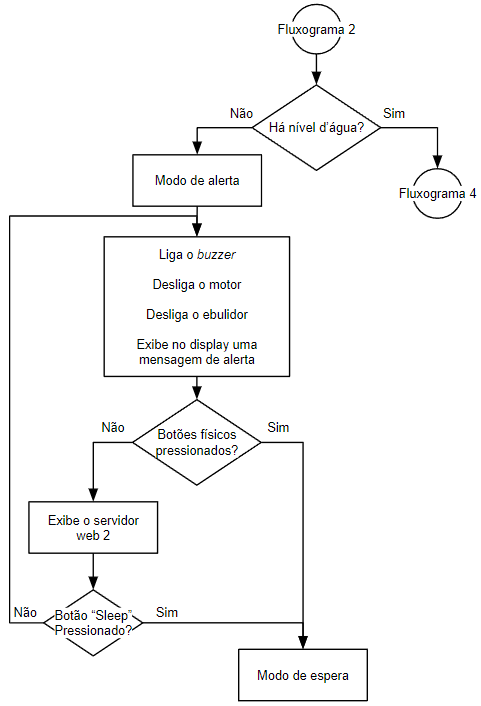
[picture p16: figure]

Fonte: Autoria própria.

Por fim, no Modo de Operação (Figuras 33, 34 e 35), tem-se a situação ideal para o funcionamento do termocirculador: posicionado em um recipiente com água. Neste modo, é possível visualizar a temperatura atual da água tanto no display quanto no servidor web, sendo que neste, pode-se também observar a temperatura atual do interior do equipamento, o status da ventoinha (ligada ou não) e a temperatura desejada pelo usuário.

Figura 33 - Fluxograma 4: Funcionamento da primeira etapa do modo de operação do algoritmo de programação desenvolvido.

Fonte: Autoria própria.

Figura 34 - Fluxograma 5: Funcionamento da segunda etapa do modo de operação do algoritmo de programação desenvolvido.

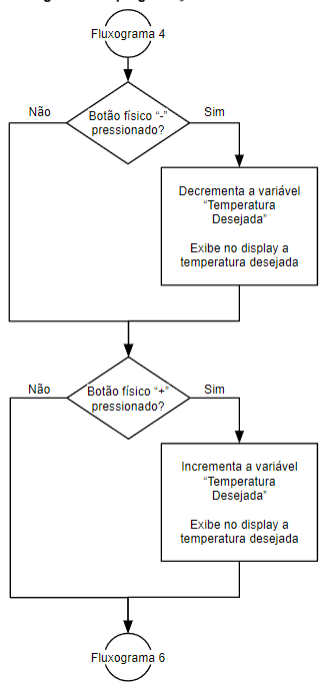
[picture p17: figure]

Fonte: Autoria própria.

Figura 35 - Fluxograma 6: Funcionamento da terceira etapa do modo de operação do algoritmo de programação desenvolvido.

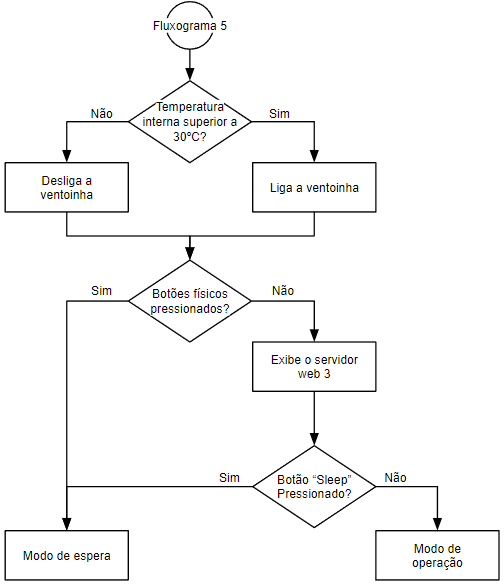
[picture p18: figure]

Fonte: Autoria própria.

4.6 | IMPLEMENTAÇÃO DO CONTROLADOR ON-OFF
| O controlador On-Off foi implementado em meio ao algoritmo de programação
do microcontrolador, ou seja, em MicroPython. Sua lógica está destacada em vermelho na Figura 33.
| Optou-se pelo uso deste tipo de controlador em razão de ter apresentado
uma baixa oscilação da temperatura da água (Gráficos 1 e 2) nos testes, variando entre valores de 59,8 a 60,4 ºC para uma temperatura desejada de 60 ºC, 99,67% e 100,67% do valor desejado, respectivamente. Desta forma, julgou-se desnecessária a necessidade de aplicação de um controlador PID para uma oscilação tão pequena, de 0,67% do valor desejado.

Gráfico 1 - Variação da temperatura da água pelo tempo.

Fonte: Autoria própria

Gráfico 2 - Zoom da variação da temperatura da água pelo tempo.

Fonte: Autoria própria

Assim, tendo como base os gráficos que descrevem o funcionamento do termocirculador desenvolvido (Gráficos 1 e 2), e a lógica seguida por seu controlador On-Off, pode-se concluir que o ebulidor se encontra ativo em, aproximadamente, 50% do tempo de operação do equipamento. Ou seja, para um funcionamento de 1 hora contínua, tem-se que o ebulidor se encontra ativado durante 30 minutos. Desta forma, como o ebulidor apresenta uma potência de 680 W, calcula-se o seu consumo energético como 340 Wh.

4.7 | FUNCIONAMENTO DO SENSOR DE TEMPERATURA INTERNA
| O sensor de temperatura interna, como mencionado anteriormente, foi
construído por meio de um circuito divisor de tensão composto por um termistor e um resistor de 1000 Ω (Figura 12).
| No entanto, para se chegar a uma equação capaz de mensurar a temperatura
interna do termocirculador a partir de um termistor, foi necessário a coleta de valores de resistência do termistor quando exposto a diversas temperaturas. Para isso, com as PCBs dispostas fora do termocirculador, utilizou-se de um simples código em MicroPython para exibir a temperatura informada pelo sensor de temperatura em sonda e a resistência do termistor no mesmo momento. Coletou-se 10 amostras de temperatura e resistência, formando o gráfico de dispersão exibido no Gráfico 3.

Gráfico 3 - Temperatura ambiente em função da resistência do termistor.

Fonte: Autoria própria

Desta forma, com o uso do software Google Sheets, obteve-se a Equação 2, de coeficiente de determinação (R²
) igual a 93,5%, capaz de calcular a temperatura interna do termocirculador em função da resistência do termistor.
Temperatura = 3415 * Resistência | (2) ⁻⁰,542
4.8 | TESTES
| O período de testes do termocirculador desenvolvido contou com a validação
do funcionamento e ajuste dos circuitos eletrônicos e do algoritmo desenvolvidos, além do preparo de 3 alimentos: bife de chorizo bovino, costelinha suína e ovos.

4.8.1 Teste dos Circuitos Eletrônicos

| O primeiro teste consistiu na validação dos circuitos eletrônicos desenvolvidos
a fim de se constatar possíveis defeitos e os reparar. Primeiramente, notou-se um defeito na placa principal. Foi necessário adicionar um botão (KEY4) entre o pino EN e o GND (Figura 36), não informado pelo datasheet do microcontrolador ESP32 e ausente em seu circuito recomendado. Este botão se fez necessário para permitir que o microcontrolador entre em modo de boot, pressionando-o após ativar o botão de reset, responsável por resetar o estado de operação do componente. Para que o microcontrolador retorne ao modo de execução, basta pressionar apenas o botão de reset.

Figura 36 - Botão responsável por colocar o microcontrolador em modo de download quando pressionado (KEY4).

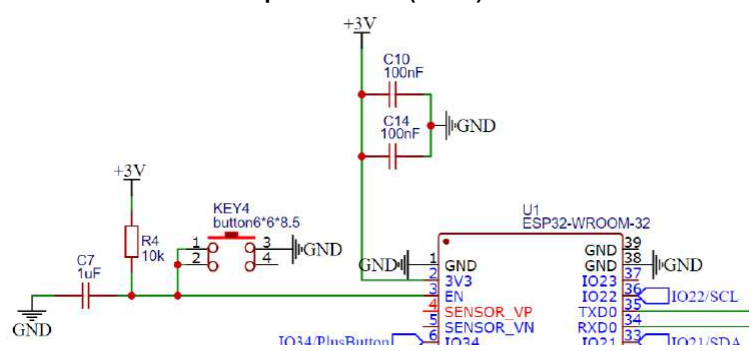
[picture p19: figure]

Fonte: Autoria própria.

Ainda, esta não foi a única falha notada durante os testes dos circuitos eletrônicos. Ao se ativar o ebulidor, notou-se que o resistor R1 e o capacitor C4 (Figura 37), localizados na placa de controle e alimentação, foram destruídos. Para se corrigir este erro, basta retirar os componentes danificados.

Figura 37 - Resistor (R1) e capacitor (C4) retirados da PCB após serem destruídos em teste.

Fonte: Autoria própria.

Devido à destruição destes componentes durante o teste mencionado, uma marca de incineração foi deixada na PCB (Fotografia 11). No entanto, felizmente, tanto o dano à placa quanto a retirada dos componentes não afetaram o funcionamento do circuito.

Fotografia 11 - Marca de incineração deixada na placa de controle e alimentação.

Fonte: Autoria própria.

Além disso, notou-se que ao ativar o ebulidor, a panela e a água, nas quais o termocirculador estava disposto, apresentavam diferença de potencial entre 7 e 14 V em relação à bancada de cozinha (Fotografia 12).

Fotografia 12 - Medição da diferença de potencial entre a panela e a bancada.

Fonte: Autoria própria.

Para solucionar tal problema, substituiu-se a tomada de 2 pinos utilizada inicialmente, por uma de 3 pinos, conectando seu terra à panela por meio de um fio com garra jacaré. Desta forma, eliminou-se a diferença de potencial entre a panela e a bancada de cozinha, como mostra a Figura 13.

Fotografia 13 - Medição da diferença de potencial entre a panela e a bancada após a adição do fio de terra.

Fonte: Autoria própria.

4.8.2 Validação do Funcionamento do Algoritmo

Este teste consistiu na observação e correção do design dos servidores web e da página de seleção e conexão da rede Wi-Fi (Figura 38), desenvolvidos com o uso de HTML, CSS e Javascript. Os servidores web são exibidos de acordo com o funcionamento do termocirculador, sendo divididos em modo de espera (servidor web 1), modo de alerta (servidor web 2) e modo de operação (servidor web 3), exibidos nas Figuras 39, 40 e 41 respectivamente.
Além disso, correções também foram realizadas no restante do algoritmo de programação, tais como a escolha da temperatura desejada padrão e o ajuste de posição dos textos exibidos no display.

Figura 38 - Página exibida pelo ponto de acesso para escolha da rede Wi-Fi.

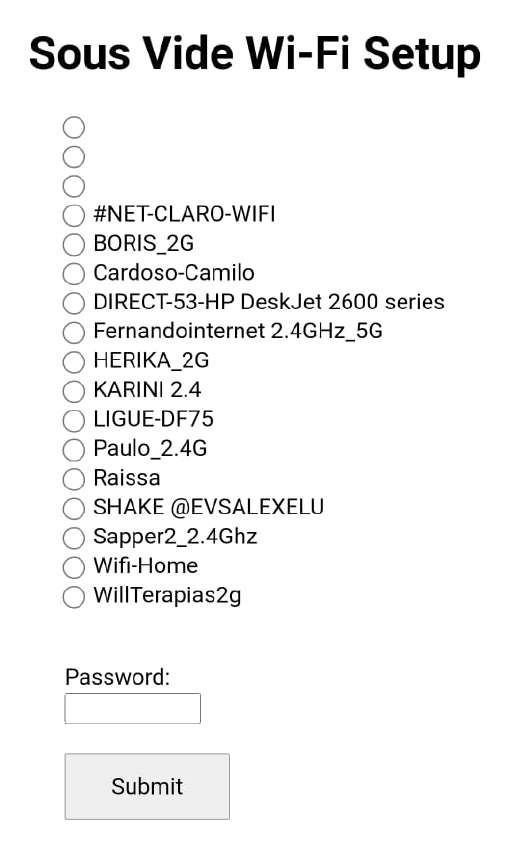
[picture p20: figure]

Fonte: Autoria própria.

Figura 39 - Servidor web 1 - Modo de espera.

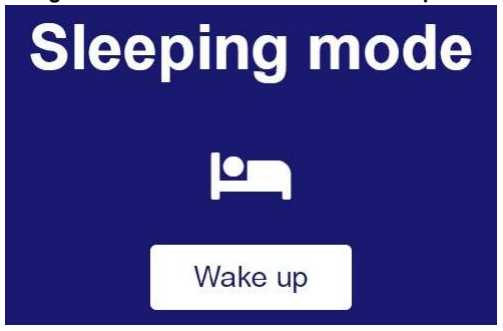
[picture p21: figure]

Fonte: Autoria própria.

Figura 40 - Servidor web 2 - Modo de alerta.

Fonte: Autoria própria.

Figura 41 - Servidor web 3 - Modo de operação.

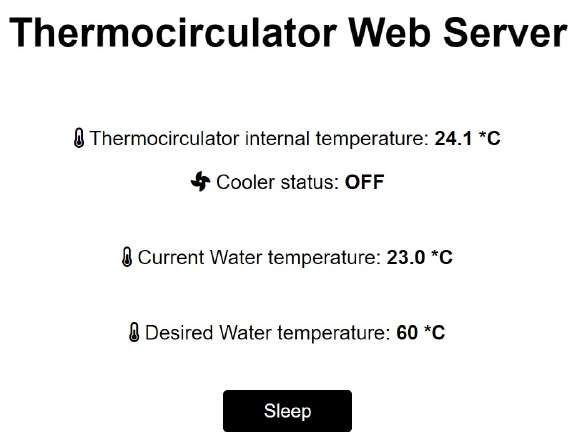
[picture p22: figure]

Fonte: Autoria própria.

4.8.3 Bife de Chorizo Bovino

Em seu livro sobre a aplicação da técnica culinária Sous Vide, Fetterman, Halm e Peabody (2016) estabeleceram 55 ºC como a temperatura correspondente a um bife ao ponto menos, 60 ºC ao ponto e 65 ºC ao ponto mais. Desta forma, a fim de se preparar um bife de chorizo bovino ao ponto menos, escolheu-se 55 ºC como temperatura desejada. A fotografia Fotografia 14 ilustra o preparo de alimentos com o uso do termocirculador desenvolvido, utilizando-se a temperatura de 60 ºC.

Fotografia 14 - Termocirculador com temperatura desejada de 60 ºC.

Fonte: Autoria própria.

Seguiu-se o sugerido por Fetterman, Halm e Peabody (2016) e, como o bife preparado possuía 1 polegada de espessura, sua cocção durou 1 hora, sendo finalizado com o uso de maçarico a gás para criação da reação de Maillard. Como resultado, obteve-se um bife suculento, extremamente saboroso e, como esperado, ao ponto menos (Fotografia 15).

Fotografia 15 - Bife de chorizo preparado ao ponto menos (55 ºC).

Fonte: Autoria própria.

4.8.4 Ovos

Quanto ao preparo de ovos não se faz necessário o uso de embalagem, uma vez que sua própria casca isola seu interior da água. A fim de averiguar a cocção da gema do ovo a diferentes temperaturas, 3 ovos foram preparados, durante 1 hora, a 60 ºC, 65 ºC e 70 ºC, dispostos da esquerda para a direita com casca na Fotografia 16 e preparados para consumo na Figura 17.

Fotografia 16 - Ovos cozidos a diferentes temperaturas (com casca).

Fonte: Autoria própria.

Fotografia 17 - Ovos cozidos a diferentes temperaturas (prontos para consumo).

Fonte: Autoria própria.

Ao se analisar os alimentos, notou-se que o ovo preparado a 60 ºC apresentava clara e gema com texturas muito menos sólidas, sendo difícil de manusear com talheres. Já o ovo preparado a 65 ºC apresentava clara com textura mais sólida do que o primeiro e gema mole, muito semelhante a ovos utilizados no preparo de ovos beneditinos. Por fim, o ovo preparado a 70 ºC apresentava clara com textura muito semelhante ao anterior, mas possuía uma gema sólida, que não escorria ao ser cortada.

4.8.5 Costelinha Suína

Além de carne bovina, a técnica culinária Sous Vide pode também ser empregada no preparo da carne de outros animais, como porco, e de durações superiores a 1 hora. Desta forma, preparou-se uma costelinha suína (Figura 18) a 70 ºC durante 4 horas, tendo em vista que se trata de um corte consideravelmente rígido. Assim como o bife de chorizo, também a finalizou com uso de maçarico.

Fotografia 18 - Costelinha suína preparada durante 4 horas.

Fonte: Autoria própria.

4.9 COMPARATIVO DO TERMOCIRCULADOR DESENVOLVIDO COM PARES DE MERCADO

| A fim de comparar as características do termocirculador desenvolvido com as
de termocirculadores comercializados, elaborou-se um comparativo com os equipamentos de entrada das fabricantes Anova Culinary, Cetro Máquinas, Chefsteps e My Sous Vide, presente no Quadro 2.

Quadro 2 - Comparativo do termocirculador desenvolvido com pares de mercado.
Característica | Termo 3D (presente trabalho) | Anova Precision Cooker Nano | Cetro SV95 | Chefsteps Joule | My Sous Vide Home User
Preço (R$) | 700,00 | 1.300,00 | 1.290,00 | 3.199,00 | 1.499,00
Potência (W) | 680 | 750 | 1200 | 1100 | 1100
Tensão (V) | 127 | 120 | 220 | 120 | 127
Dimensão lateral (cm) | 7 x 7 | 7,8 x 10,5 | 14,5 x 13 | 4,83 x 4,83 | 6 x 7,5
Altura (cm) | 18,5 | 32,5 | 32 | 27,94 | 36,50
Peso (kg) | 0,40 | 0,63 | - | 0,58 | 2,30
Monitoramento via Wi-Fi | Sim | Sim | Não | Sim | Não
Controle via Wi-Fi | Não | Sim | Não | Sim | Não
Controle via Bluetooth | Não | Sim | Não | Sim | Não
Tipo de fixação | Base magnética | Suporte | Suporte | Base magnética | Suporte
Visor e botões físicos | Sim | Sim | Sim | Não | Sim

Fonte: Anova Culinary (2022a), Cetro Máquinas (2022b), Chefsteps (2022) e My Sous Vide (2023).

Ao se analisar o Quadro 4, nota-se, primeiramente, que o termocirculador desenvolvido neste trabalho apresenta um custo inferior ao de seus concorrentes, cumprindo o seu requisito de possuir um custo reduzido. Além disso, optou-se por um ebulidor de 680 W pois os de potência superiores a 1000 W possuíam mais do que o dobro da altura do utilizado, possibilitando assim, um termocirculador mais compacto. Destaca-se também, que o equipamento desenvolvido possui a função de monitoramento via Wi-Fi, ausente em alguns modelos comerciais.

4.10 DESENVOLVIMENTO DE UMA EMPRESA FICTÍCIA

No Brasil, estima-se que 52,2% dos empregos de carteira assinada são gerados por empresas de pequeno porte, sendo que estas correspondem a 99,1%

dos empreendimentos formais do país e são responsáveis por 20% de seu Produto Interno Bruto (PIB) (MESQUITA, 2018). Segundo pesquisa do Sebrae (Serviço Brasileiro de Apoio às Micro e Pequenas Empresas) (2016), entre as empresas fundadas em 2012, apenas 76,6% delas sobreviveram após 2 anos de operação. Quando se observa empresas fundadas entre 2008 e 2009, o percentual de negócios sobreviventes cai consideravelmente (Gráfico 4).

Gráfico 4 - Taxa de sobrevivência de empresas em 2 anos de operação de acordo com seu ano de fundação.

Fonte: Sebrae (2016).

Ainda, segundo Olivan (2021), apenas 37,6% das empresas fundadas em 2014 sobreviveram até 2019. Segundo esta mesma pesquisa, há correlação positiva entre a permanência da empresa no mercado e o seu tamanho, ou seja, quanto maior o porte da empresa, maior a taxa de sobrevivência.
Segundo Viana (2022), um dos principais fatores que influenciam no fechamento precoce de empresas é a falta de planejamento do negócio. Desta forma, nota-se a necessidade de se planejar a abertura da empresa, elevando suas chances de sobrevivência ao longo dos anos.
Assim, levando em consideração a importância do planejamento empresarial para a saúde futura do negócio, e pensando no desenvolvimento completo de um termocirculador, decidiu-se elaborar uma empresa fictícia responsável por sua pesquisa, produção e comercialização. Desta forma, desenvolveu-se um modelo de negócio, um plano de negócio e a marca da empresa.

4.10.1 Modelo de Negócio

Para a elaboração do modelo de negócio da empresa fictícia (Figura 42), baseou-se no livro de Osterwalder e Pigneur (2011). O Modelo de Negócios Canvas foi criado durante a tese de doutorado do professor e pesquisador suíço Alexander Osterwalder, em 2004. Atualmente, é utilizado por empresas de todo o mundo, como Google, Spotify e Amazon (MARTINS, 2021).

Figura 42 - Modelo de Negócios Canvas elaborado.

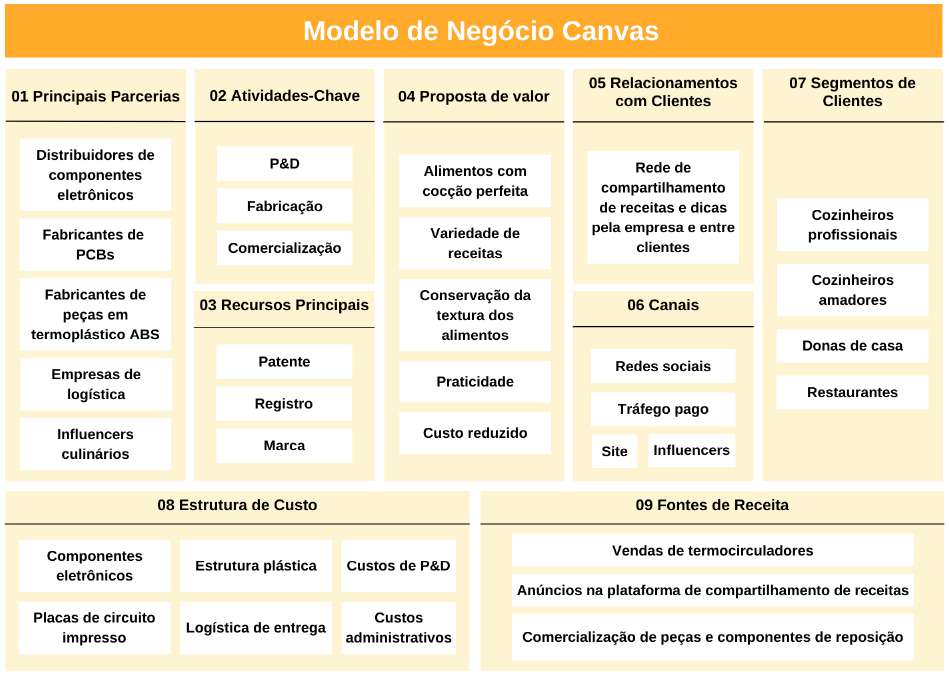
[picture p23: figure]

Fonte: Autoria própria.

4.10.2 Plano de Negócios

O plano de negócios busca descrever os objetivos de uma empresa, bem como quais passos devem ser seguidos para alcançá-los. Desta forma, um plano de negócios diminui os riscos e as incertezas que permeiam o início de uma empresa, e permite identificar e corrigir erros ainda no papel, evitando cometê-los durante o funcionamento. Ainda, um plano de negócios ajuda a concluir se a ideia de uma empresa é viável, buscando informações sobre o ramo, os produtos e os serviços trabalhados, os fornecedores e os clientes, além de expor os pontos fortes e fracos do futuro negócio (SEBRAE, 2013).
Assim, para a elaboração do plano de negócios da empresa fictícia relacionada a este trabalho, seguiu-se a metodologia proposta pelo Sebrae, disponível no manual: Como elaborar um plano de negócios (SEBRAE, 2013). Segundo esta metodologia, um plano de negócios consiste em 7 tópicos principais: sumário executivo, análise de mercado, plano de marketing, plano operacional, plano financeiro, construção de cenários e avaliação estratégica.

4.10.2.1 Sumário executivo

O sumário executivo se trata de um resumo do plano de negócios, contendo os pontos mais importantes.

4.10.2.1.1 | O conceito do negócio
Esta | empresa | desenvolverá | (P&D), | fabricará | e | comercializará
termocirculadores para seu público alvo: cozinheiros amadores e profissionais, donas de casa e restaurantes, com foco no primeiro grupo. Seus únicos produtos comercializados serão termocirculadores, no entanto, sua fonte de receita também abarca a comercialização de peças e componentes de reposição e o aluguel de espaços para anúncios em sua plataforma de compartilhamento de receitas entre usuários.
O seu principal objetivo será tornar a prática da técnica culinária Sous Vide mais acessível a cozinheiros amadores e pequenos restaurantes que, geralmente, não dispõem de renda suficiente para adquirir um termocirculador profissional comercializado a altos valores por seus competidores de mercado atuais. Os diferenciais de seus termocirculadores serão o custo-benefício, a conexão wireless com o usuário e a facilidade de uso dos equipamentos.
Para a abertura da empresa, estima-se a necessidade de investimento de um capital igual a R$ 23.061,00.

### 4.10.2.1.2 O produto

O primeiro modelo de termocirculador desenvolvido pela empresa possuirá como destaques: conexão Wi-Fi, display OLED de 3 polegadas para exibição de informações ao usuário, estrutura em plástico ABS, potência de 680 W e tensão de operação doméstica de 127 V. Suas dimensões serão compactas (7 x 7 x 18,5 cm), ideal para trabalhar com recipientes de diversos tamanhos, presentes em uma cozinha amadora.
Planeja-se que outros modelos sejam desenvolvidos futuramente, podendo variar a potência e tensão de operação, tipo e tamanho do display, dimensões do produto e tipo de conexão wireless (Bluetooth ou Wi-Fi).

### 4.10.2.1.3 Equipe de gestão

A equipe de gestão será composta, inicialmente, apenas por seu fundador, que dispõe de conhecimentos nas áreas de engenharia elétrica e eletrônica, economia e finanças.

### 4.10.2.1.4 Missão

Desenvolvimento, fabricação e comercialização de termocirculadores para cozinheiros amadores e profissionais, donas de casa e restaurantes.

4.10.2.2 Análise de mercado

O mercado de termocirculadores cresceu nos últimos anos graças à difusão e popularização da técnica culinária Sous Vide por meio da internet, ganhando espaço nas cozinhas domésticas. É composto por empresas como Anova Culinary, Chefsteps e a brasileira Cetro Máquinas.

### 4.10.2.2.1 Cliente

Uma pesquisa de mercado foi realizada a fim de se obter informações relevantes a respeito do perfil dos clientes da empresa. Para isso, obteve-se dados de donos e potenciais consumidores de termocirculadores. A pesquisa foi conduzida por meio da criação de um formulário, seguido de sua divulgação em grupos do Facebook sobre Sous Vide e na seção de comentários de vídeos culinários da plataforma YouTube relacionados a esta técnica culinária. Os meios de divulgação se tratavam de comunidades majoritariamente de língua inglesa, sendo necessário elaborar o formulário em inglês e tratar de valores monetários em dólar.
O formulário coletou informações durante 2 meses, de 26/01/2023 a 31/03/2023, recebendo um total de 38 respostas. Obteve-se informações relevantes a respeito do perfil dos clientes interessados no produto desenvolvido, as quais são indicadas do Gráfico 5 ao Gráfico 14.

Gráfico 5 - Faixa etária.

Fonte: Autoria própria.

Gráfico 6 - Renda em milhares de dólares.

Fonte: Autoria própria.

Gráfico 7 - Continente de residência.

Fonte: Autoria própria.

Gráfico 8 - Alimento mais preparado com o equipamento.

Fonte: Autoria própria.

Gráfico 9 - Maior atrativo para a compra do equipamento.

Fonte: Autoria própria.

Gráfico 10 - Valor máximo que pagaria em um termocirculador.

Fonte: Autoria própria.

Gráfico 11 - Fabricante de termocirculadores de preferência.

Fonte: Autoria própria.

Gráfico 12 - Se considera importante a presença de conexão wireless no equipamento.

Fonte: Autoria própria.

Gráfico 13 - Se considera importante a disponibilidade de uma rede de compartilhamento de receitas entre usuários.

Fonte: Autoria própria.

Gráfico 14 - Uso profissional ou amador do equipamento.

Fonte: Autoria própria.

Desta forma, pôde-se formar a persona consumidora deste equipamento, sendo ela de meia idade (50% das respostas entre 41 e 60 anos), de renda elevada (36,80% dos participantes recebem mais de cem mil dólares por ano) e residente da América do Norte (55,3% dos votos). Quanto às suas opiniões, tem-se que prefere utilizar o termocirculador para o preparo de cortes bovinos (preferência de 60,5% dos votantes), tendo o adquirido em razão da facilidade de se obter uma cocção perfeita (76,3% dos votos), pagaria no máximo 200 dólares pelo equipamento (93,4% dos votos), possui preferência pela marca Anova Culinary (63,2% dos votos) e utiliza o equipamento de forma amadora (94,7%). Surpreendentemente, 60,5% dos votantes não consideraram importante a presença de conexão wireless no equipamento.

### 4.10.2.2.2 Concorrentes

Este mercado é composto majoritariamente por empresas estrangeiras, com destaque para as americanas Anova Culinary e Chefsteps. Quanto ao mercado nacional, pode-se destacar a empresa Cetro Máquinas, que dispõe de equipamentos profissionais e amadores em seu catálogo.
Fundada no ano de 2012, a Chefsteps está sediada em Seattle (EUA), possui como missão ajudar pessoas a cozinhar de forma inteligente. Possui como principal equipamento, o termocirculador Chefsteps Joule, anunciado em 2016 (HATCH, 2016). Além da qualidade de seus equipamentos, agrega valor aos clientes e se diferencia dos concorrentes por meio da disponibilização de aulas de culinária e receitas de diversos alimentos (CHEFSTEPS, 2022). Seu produto de entrada se trata do Joule White Polycarbonate, no valor de U$ 199,99 (BREVILLE, 2022). Já como seu produto topo de linha, tem-se o Joule Stainless Steel, comercializado por U$ 249,99 (BREVILLE, 2022). Seus termocirculadores dispõem de base magnética para fixação ao recipiente.
Já a empresa Anova Culinary, foi fundada no ano de 2013, possui sede em
San | Francisco | (EUA), | e | comercializa | equipamentos | culinários | como
termocirculadores, fornos e seladoras a vácuo. Ainda em 2013 anunciou seu primeiro e, ainda hoje, principal produto, o Anova Precision Cooker (ANOVA, 2019). Foi adquirida pela multinacional sueca Electrolux em 2017 pelo valor de 250 milhões de dólares (ELECTROLUX, 2017). Seu produto de entrada se trata do Precision Cooker Nano, no valor de U$ 99,99 (ANOVA CULINARY, 2022a). Já como seu produto topo de linha, tem-se o Precision Cooker Pro, comercializado por U$ 399,99 (ANOVA CULINARY, 2022b).
Por sua vez, a brasileira Cetro Máquinas está localizada em Bauru-SP (Brasil), e foi fundada no ano de 2012. Iniciou com o comércio de máquinas de embalar produtos e, atualmente, conta com mais de 250 funcionários e mais de 600 máquinas em seu catálogo, entre elas termocirculadores e water ovens (BONINI, 2021) Seu produto de entrada se trata do SV95, no valor de R$ 1.290,00 (CETRO

MÁQUINAS, 2022b). Já como seu termocirculador topo de linha, tem-se o SV100, comercializado por R$ 3.290,00 (CETRO MÁQUINAS, 2022c).

### 4.10.2.2.3 Fornecedores

Entre os fornecedores necessários para as operações da empresa, destacam-se 3 cujos produtos estão estritamente relacionados a fabricação dos termocirculadores:
- Distribuidores de componentes eletrônicos;
- Fabricantes de placas de circuito impresso;
- Fabricantes de filamentos para impressão 3D.

Entre distribuidores de componentes eletrônicos, destacam-se Digi-Key, Mouser Electronics e ICSuperman, empresas que possuem disponível em seu estoque todos os componentes necessários para os circuitos presentes nos termocirculadores a serem fabricados. Já quanto aos fabricantes de placas de circuito impresso, temos com destaque a JLCPCBs, que oferece um rápido e fácil processo de solicitação de fabricação de PCBs. Por fim, quanto aos fabricantes de filamentos para impressão 3D, pode-se citar a empresa 3D Lab, que conta com filamentos de diferentes materiais e de muita qualidade a preços reduzidos.

4.10.2.3 Plano de marketing

Atualmente, os termocirculadores presentes no mercado possuem um alto valor comercial, impedindo a sua aquisição por cozinheiros amadores de baixa renda e pequenos restaurantes. Pensando nisso, a estratégia de marketing desta empresa objetiva atender esta demanda reprimida, ofertando ao mercado termocirculadores de custo reduzido em relação aos seus concorrentes e de simples funcionamento.
A prospecção de clientes ocorrerá por meio das redes sociais da empresa, combinado a estratégias de tráfego pago e parcerias com influencers e programas culinários. As vendas serão realizadas integralmente de forma online, por meio de site próprio e anúncios em marketplaces, tais como Mercado Livre e Amazon, reduzindo os custos necessários para a abertura de uma loja física.

### 4.10.2.3.1 Preço

Os componentes eletrônicos serão adquiridos em atacado por meio de um dos fornecedores mencionados anteriormente, em razão da redução de custo. Já as placas de circuito impresso serão fabricadas em grandes quantidades por meio da empresa JLC PCBs. Desta forma, com base nos valores dos componentes adquiridos para a construção do equipamento desenvolvido neste trabalho, toda a eletrônica do termocirculador terá um custo de fabricação igual a R$ 205,09 por unidade, discriminado no Quadro 3.

Quadro 3 - Custos de fabricação dos circuitos eletrônicos por termocirculador.
Insumo | Quantidade | Custo unitário | Custo total
Botão | 2 | R$ 0,56 | R$ 1,12
Buzzer | 1 | R$ 2,71 | R$ 2,71
Cabos conectores de 2 vias | 4 | R$ 1,46 | R$ 2,92
Cabos conectores de 3 vias | 4 | R$ 1,88 | R$ 3,76
Capacitor | 4 | R$ 0,05 | R$ 0,20
Conector borne | 2 | R$ 0,61 | R$ 1,22
Conversor AC-DC | 1 | R$ 18,24 | R$ 18,24
Display OLED | 1 | R$ 33,55 | R$ 33,55
Ebulidor | 1 | R$ 37,90 | R$ 37,90
ESP32-WROOM-32 | 1 | R$ 45,00 | R$ 45,00
LED | 1 | R$ 0,14 | R$ 0,14
Mini botão | 2 | R$ 0,39 | R$ 0,78
Motor CC | 1 | R$ 10,00 | R$ 10,00
Optoacoplador | 1 | R$ 3,46 | R$ 3,46
Resistor | 9 | R$ 0,04 | R$ 0,36
Soquete | 5 | R$ 0,11 | R$ 0,55
Sensor de nível d’água | 1 | R$ 3,04 | R$ 3,04
Sensor de temperatura | 1 | R$ 14,90 | R$ 14,90
Termistor | 1 | R$ 0,28 | R$ 0,28
Transistor | 2 | R$ 0,08 | R$ 0,16

TRIAC | 1 | R$ 3,46 | R$ 3,46
Ventoinha | 1 | R$ 13,34 | R$ 13,34
Placa de controle e alimentação | 1 | R$ 4,00 | R$ 4,00
Placa principal | 1 | R$ 4,00 | R$ 4,00
Custo de fabricação dos circuitos eletrônicos | R$ 205,09

Fonte: Autoria própria.

A fabricação da estrutura do equipamento será realizada pela própria empresa, inicialmente em menor escala e por meio de impressão 3D em plástico ABS, com valor de R$ 75,09 por unidade e discriminado no Quadro 4.

Quadro 4 - Custos de fabricação da estrutura plástica por termocirculador.
Insumo | Quantidade | Custo unitário | Custo total
Hélice (6,35 g) | 1 | R$ 0,52 | R$ 0,52
Imãs | 4 | R$ 10,32 | R$ 41,28
Parafusos hexagonais | 8 | R$ 0,49 | R$ 3,92
Parafusos | 20 | R$ 0,49 | R$ 9,80
Porcas | 2 | R$ 0,49 | R$ 0,98
Parte inferior (99,34 g) | 1 | R$ 7,18 | R$ 7,18
Parte superior (47,63 g) | 1 | R$ 2,96 | R$ 2,96
Tampa inferior 1 (13,61 g) | 1 | R$ 0,66 | R$ 0,66
Tampa inferior 2 (4,54 g) | 1 | R$ 0,56 | R$ 0,56
Tampa medial (14,06 g) | 1 | R$ 1,29 | R$ 1,29
Suporte ebulidor (6,80 g) | 1 | R$ 0,49 | R$ 0,49
Suporte do sensor de temperatura (0,45g) | 2 | R$ 0,03 | R$ 0,06
Energia gasta na impressão 3D (Anet ET4 - 240 W) | 26 horas e 55 minutos | R$ 0,22 | R$ 5,95
Custo de fabricação da estrutura plástica | R$ 75,09

Fonte: Autoria própria.

Desta forma, os termocirculadores comercializados pela empresa terão um custo de fabricação igual a R$ 280,18 por unidade. Além dos custos de produção do produto, deve-se considerar também os impostos incidentes sobre o seu valor final de venda: ICMS (19%) e IPI (6,5%)
Assim, estima-se um valor de venda de R$ 700,00 por termocirculador, situando-se abaixo do valor praticado por empresas concorrentes (superiores a R$ 1.000,00), mantendo sua proposta inicial de custo reduzido ao cliente e apresentando um custo de fabricação de R$ 280,18 e impostos iguais a de R$ 178,50, ou seja, um custo total de R$ 458,68. Desta forma, estima-se um lucro bruto igual a R$ 241,32 por unidade vendida, representando uma margem de lucro bruto igual a 34,50 %.
Assim, tem-se o valor final de venda dos termocirculadores composto por R$ 280,18 (40,00%) referente aos custos de fabricação, R$ 178,50 (25,50%) referente aos impostos incidentes sobre a venda do produto e R$ 241,32 (34,50%) referentes ao lucro por unidade vendida (Gráfico 15).

Gráfico 15 - Composição do valor final de venda.

Fonte: Autoria própria.

4.10.2.4 Plano operacional

Inicialmente, as operações da empresa serão desempenhadas e controladas por seu único membro, com este atuando desde a etapa de projetos e planejamento, até a encomenda dos componentes eletrônicos e placas de circuito impresso e montagem do termocirculador. Desta forma, no início certos processos serão terceirizados até que, com o crescimento das operações da empresa, ocorra a expansão da equipe.

4.10.2.5 | Plano financeiro
4.10.2.5.1 | Estimativa dos investimentos fixos

Diante da possibilidade de iniciar as operações da empresa com certos processos terceirizados, tem-se uma grande redução do investimento fixo inicial, que corresponde ao investimento nos bens necessários para que a empresa funcione de maneira adequada (SEBRAE, 2013). Assim, estima-se a necessidade de um investimento fixo no valor de R$ 8.000,00, sendo R$ 3.000,00 direcionados a aquisição de um notebook de uso profissional, R$ 4.500,00 direcionados a compra de uma impressora 3D de alta qualidade e R$ 500,00 direcionados a aquisição de ferramentas para o manuseio e montagem dos termocirculadores (Quadro 5).

Quadro 5 - Investimento fixo.
Notebook | R$ 3.000,00
Impressora 3D | R$ 4.500,00
Ferramentas | R$ 500,00
Investimento fixo | R$ 8.000,00
Fonte: Autoria própria.

### 4.10.2.5.2 Capital de giro

Segundo Sebrae (2013), o capital de giro representa os recursos necessários para o funcionamento normal da empresa, como matéria prima. Assim, projeta-se a necessidade de um investimento em capital de giro inicial igual a R$ 14.061,00, considerando o estoque de componentes, placas de circuito impresso e estruturas para a produção de 50 unidades iniciais de termocirculadores (Quadro 6).

Quadro 6 - Investimento em capital de giro inicial.
Aquisição dos componentes eletrônicos iniciais | R$ 9.415,00
Fabricação de PCBs iniciais | R$ 400,00
Fabricação das estruturas iniciais | R$ 4.247,00
Investimento total em capital de giro inicial | R$ 14.061,00
Fonte: Autoria própria.

### 4.10.2.5.3 Investimentos pré-operacionais

Como a empresa iniciará suas operações em na residência de seu fundador, não haverá a necessidade de despesas com reformas ou aquisição de um local. Ainda, como a empresa iniciará contando com apenas seu fundador na equipe, será registrada como MEI (Micro Empreendedor Individual) sem custos. Desta forma, como custos pré-operacionais tem-se apenas o custo inicial de divulgação definido como R$ 1.000,00, valor suficiente para divulgar os produtos da empresa e seus canais de vendas nas redes sociais.

### 4.10.2.5.4 Investimento total

Somando-se as três divisões de investimento mencionadas anteriormente, chega-se ao investimento inicial total de R$ 23.061,00, que será obtido a partir de recursos próprios do fundador (Quadro 7).

Quadro 7 - Divisão do investimento inicial total.
Investimento fixo | R$ 8.000,00
Investimento em capital de giro | R$ 14.061,00
Investimentos pré-operacionais | R$ 1.000,00
Investimento total | R$ 23.061,00
Fonte: Autoria própria.
4.10.2.6 | Avaliação estratégica
4.10.2.6.1 | Análise SWOT

Com base na matriz SWOT elaborada (Figura 43), determinou-se os principais fatores críticos para o início das operações da empresa. Alguns dificultam seu sucesso final, como o setor apresentar concorrência já consolidada, dificuldade de diferenciação e a existência de poucos consumidores. Alguns favorecem, como o baixo investimento inicial e o público alvo pouco explorado.

Figura 43 - Matriz SWOT.

Fonte: Autoria própria.

4.10.3 A Marca

A marca da empresa foi elaborada levando em consideração aspectos que a ligue diretamente ao seu produto, termocirculadores. Desta forma, o nome escolhido para a nomear foi Termo 3D, em referência ao método de fabricação da estrutura plástica dos equipamentos. Ainda, utilizando as cores bordô e salmão, criou-se a seguinte logo para estampar os produtos e comerciais da empresa (Figura 44).

Figura 44 - Logo da empresa fictícia.

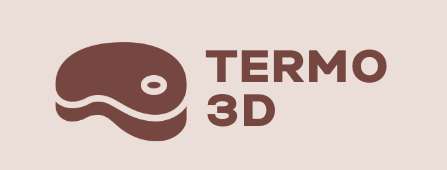
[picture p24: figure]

Fonte: Autoria própria.

4.10.4 Conclusão Sobre a Viabilidade do Negócio

Após o desenvolvimento de todo o planejamento empresarial, contando com modelo de negócios, plano de negócios e marca, uma análise cuidadosa acerca da viabilidade do negócio foi feita. Levou-se em consideração, principalmente, a análise SWOT elaborada, com foco para as seguintes ameaças: setor com empresas consolidadas e poucos consumidores, além da seguinte fraqueza: dificuldade de diferenciação do produto, que quando observadas individualmente, já apresentam algum perigo ao negócio. No caso analisado, os três ocorrem simultaneamente, apresentando muito mais perigo, tanto no início quanto durante as operações da empresa, independentemente de quantos anos se passar.
Assim, com poucos clientes por se tratar de um utensílio culinário pouco conhecido e aplicável a uma técnica culinária específica, combinado a um mercado já composto por empresas famosas e consolidadas mundialmente, como Anova Culinary - pertencente à gigante Electrolux - e ChefSteps, conclui-se que a abertura de uma empresa desenvolvedora e fabricante de termocirculadores é inviável diante do contexto apresentado.

### 5 CONCLUSÃO

Com a realização deste trabalho, cumpriu-se todos os objetivos estabelecidos inicialmente: desenvolvimento e execução dos circuitos eletrônicos e da estrutura do termocirculador, elaboração de um algoritmo de programação para o microcontrolador em MicroPython, contando com a implementação de um controlador On-Off para a manutenção da temperatura constante da água e planejamento de uma empresa fictícia responsável pelo desenvolvimento, fabricação, comercialização e distribuição do equipamento.
Como resultado final, obteve-se um equipamento compacto, muito menor do que seus pares de mercado, capaz de manter a temperatura da água constante, de baixo custo, controlado por meio de botões físicos e monitorado via servidor web, funcionalidade esta ausente em certos modelos comercializados. No entanto, infelizmente, a conclusão acerca da viabilidade do negócio elaborado por meio da empresa fictícia não foi a desejada, inviabilizando a abertura do mesmo. Apesar disso, pode-se concluir que este trabalho foi um sucesso, culminando em um produto de perfeito funcionamento: um termocirculador aplicado à técnica culinária Sous Vide.
Para trabalhos futuros, há a possibilidade de melhorar os servidores web elaborados para este equipamento, e permitir, além do monitoramento, o controle da temperatura da água desejada por meio de botões virtuais. A substituição do motor com hélice por uma bomba d’água também é uma possibilidade, além da troca do ebulidor de 680 W por um de potência superior a 1000 W. Ainda, pode-se optar pelo uso de outro sensor de nível d'água, uma vez que o utilizado neste trabalho não emite uma tensão igual a zero quando retirado da água, pois sua superfície permanece úmida durante alguns minutos. A substituição dos dois botões físicos e do display OLED por um display com suporte a touchscreen, aproximaria ainda mais este termocirculador de seus pares de mercado.

REFERÊNCIAS

3D | LAB. | Filamento | ABS | Premium | Preto. | Disponível | em:
https://3dlab.com.br/produto/filamento-abs-premium-preto/. Acesso em: 31 mar. 2023a.
3D | LAB. | Filamento | PETG | Branco. | Disponível | em:
https://3dlab.com.br/produto/filamento-petg-branco/. Acesso em: 31 mar. 2023b.
3D | LAB. | Filamento | PLA | Premium | Branco. | Disponível | em:
https://3dlab.com.br/produto/filamento-pla-branco/. Acesso em: 31 mar. 2023c.

ALIEXPRESS. 10 pcs LM1117T-3.3 LM1117T LM1117 Low Dropout Voltage Regulator 3.3 V. Disponível em: https://pt.aliexpress.com/item/32421177118.html. Acesso em: 17 mar. 2023.

Anova Company Fact Sheet. San Francisco. 2019. 1 p.

ANOVA CULINARY. Anova Precision Cooker Nano. Disponível em: https://anovaculinary.com/products/anova-precision-cooker-nano. Acesso em: 29 nov. 2022a.

ANOVA | CULINARY. | Anova | Precision | Cooker | Pro. | Disponível | em:
https://anovaculinary.com/products/anova-precision-cooker-pro. Acesso em: 29 nov. 2022b.

BALDWIN, Douglas E. Sous vide cooking: a review. International Journal Of Gastronomy And Food Science, [S.L.], v. 1, n. 1, p. 15-30, Jan. 2012. Elsevier BV.

BONINI, Raphael. Bauruense começou testando máquinas na garagem e hoje
planeja | abrir | unidade | nos | EUA. | 2021. | Disponível | em:
https://www.socialbauru.com.br/2021/10/04/bauruense-testando-maquinas-garagem-hoje-planeja-abrir-unidade-eua/. Acesso em: 29 nov. 2022.

BORGES, António M. F. Desenvolvimento de um sistema electrónico de aquecimento para “sous vide”. 2019. 105 p. Dissertação (Mestrado) - Faculdade de Ciências e Tecnologia, Universidade Nova de Lisboa, Lisboa, 2019.

BOYLESTAD, Robert; NASHELSKY, Louis. Dispositivos eletrônicos e teoria de circuitos. 11. ed. São Paulo: Pearson Education do Brasil, 2013. 782 p.

BREVILLE. | Joule | Sous | Vide | - | Stainless | Steel. | Disponível | em:
https://www.breville.com/us/en/products/sous-vide/cs10001.html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
31. Acesso em: 29 nov. 2022.

BREVILLE. Joule Sous Vide - White Polycarbonate. Disponível em: https://www.breville.com/us/en/products/sous-vide/cs20001.html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
1. Acesso em: 29 nov. 2022.

CARDOSO, Matheus. Como Funciona o Controlador ON/OFF? 2020. Disponível em: https://edu.ieee.org/br-ufcgras/como-funciona-o-controlador-on-off/. Acesso em: 28 mar. 2023.

CETRO MÁQUINAS. Termocirculador Sous Vide Constantine - Bivolt. Disponível em:
https://www.cetro.com.br/termocirculador-sous-vide-constantine/p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. Acesso em: 14 nov. 2022a.

CETRO MÁQUINAS. Termocirculador Sous Vide SV95. Disponível em: https://www.cetro.com.br/termocirculador-sous-vide-sv95/p?idsku=896&gclid=Cj0KC QiAyMKbBhD1ARIsANs7rEGFOVaW92XiSQNPcTFA1xo7X5jMv2UdKTyj8sCQZXco v-8fDur-mqkaAiwVEALw_wcB. Acesso em: 14 nov. 2022b.

CETRO MÁQUINAS. Termocirculador Sous Vide SV 100. Disponível em: https://www.cetro.com.br/termocirculador-sous-vide-sv-100/p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 4yd 2kf4PHBrwaArINEALw_wcB. Acesso em: 14 nov. 2022c.

CHEFSTEPS. Welcome to ChefSteps!: we are here to help you go from curious cook to confident in the kitchen.. We’re here to help you go from curious cook to confident in the kitchen. Disponível em: https://www.chefsteps.com/. Acesso em: 14 nov. 2022.

CREED, Philip G.; REEVE, William. Principles and applications of sous vide processed foods. Sous Vide And Cook Chill Processing For The Food Industry. Gaithersburg. p. 25-56. Ago. 1998.

DARAZ. USB To Serial USB TO UART TTL SERIAL CP2102 Module. Disponível em:
https://www.daraz.pk/products/usb-to-serial-usb-to-uart-ttl-serial-cp2102-module-i147 852162.html. (https://www.daraz.pk/products/usb-to-serial-usb-to-uart-ttl-serial-cp2102-module-i147852162.html) Acesso em: 17 mar. 2023.

DS18X20: DS18B20 temperature sensor driver. DS18B20 temperature sensor driver.
Disponível | | em:
https://mpython.readthedocs.io/en/master/library/mPython/ds18x20.html. Acesso em: 11 abr. 2023.

ELECTROLUX to acquire fast-growing smart kitchen appliance company Anova.
2017. | Disponível | em:
https://www.electroluxgroup.com/en/electrolux-to-acquire-fast-growing-smart-kitchen-appliance-company-anova-23189. Acesso em: 29 nov. 2022.

ESPRESSIF SYSTEMS. ESP32-WROOM-32 Datasheet. [Datasheet]. Manufacturer: Espressif Systems, 2021.

ON SEMICONDUCTOR. MOC3023: Optocoupler, Phototriac Output, Zero Crossing, DIP-6. [Datasheet]. Manufacturer: ON Semiconductor, 2018.

FERRANDO, Daniel; ARAUJO, John Welvins Barros de; KAKUNO, Edson Massayuki. Controle de Temperatura PID com Arduino. In: SALÃO INTERNACIONAL DE ENSINO, PESQUISA E EXTENSÃO - SIEPE, 9., 2017, Santana do Livramento. Anais. Santana do Livramento: Unipampa, 2017. p. 1-7.

FETTERMAN, Lisa Q.; HALM, Meesha; PEABODY, Scott. Sous Vide At Home: the modern technique for perfectly cooked meals. Berkeley: Ten Speed Press, 2016. 385 p.

FRANCISQUINI, Júlia D'Almeida et al. REAÇÃO DE MAILLARD: uma revisão. Revista do Instituto de Laticínios Cândido Tostes, [S.L.], v. 72, n. 1, p. 48, 21 nov. 2017. Lepidus Tecnologia. http://dx.doi.org/10.14295/2238-6416.v72i1.541.

GALVANI, Yohanna. Filamentos para impressora 3D: entenda como funcionam e escolha o melhor para você. Entenda como funcionam e escolha o melhor para você. Disponível em: https://www.filipeflop.com/blog/filamentos-para-impressora-3d/. Acesso em: 20 ago. 2022.

HAMMELRATH, Robert. Driver for the SH1106 display. 2023. Disponível em: https://github.com/robert-hh/SH1106. Acesso em: 11 abr. 2023.

HATCH, | Amy. | ChefSteps | Announces | Joule. | 2016. | Disponível | em:
https://www.chefsteps.com/chefsteps-debuts-joule#:~:text=Founded%20in%202012 %2C%20ChefSteps%20is,techniques%2C%20tools%2C%20and%20resources.. Acesso em: 29 nov. 2022.

INSTITUTE OF PRINTED CIRCUITS. IPC-2221A: Generic Standard on Printed Board Design. Northbrook: Ipc, 2003. 124 p.

JOOM. Conversor Ac-Dc Módulo de Fonte de Alimentação Ac 110V 220V 230V
Para | 5V | 12V | 24V | Comutação. | Disponível | em:
https://www.joom.com/pt-br/products/5c94a21d8b2c37010199b5ba. Acesso em: 17 mar. 2023.

MACHINE: Functions related to the hardware. 2023. Disponível em: https://docs.micropython.org/en/latest/library/machine.html. Acesso em: 11 abr. 2023

MARCOTTI, João V. P.; NASCIMENTO, Erinaldo S. Desenvolvimento de um termocirculador aplicado à técnica culinária Sous Vide. In: XII EPCC -ENCONTRO INTERNACIONAL DE PRODUÇÃO CIENTÍFICA DA UNICESUMAR, 2021, Maringá. Anais Eletrônico XII EPCC. Maringá: Unicesumar, 2021. 4p.

MARTINS, Wendel. O que é o Business Model Canvas e como usar a técnica na prática? 2021. Disponível em: https://senno.ai/business-model-canvas/. Acesso em: 14 nov. 2022.

MATH: Mathematical functions. Mathematical functions. 2023. Disponível em: https://docs.micropython.org/en/latest/library/math.html. Acesso em: 11 abr. 2023.

MESQUITA, Laís Gonçalves. Elaboração Do Plano De Gestão De Uma Empresa Fictícia De Serviços De Automação. 2018. 57 f. TCC (Graduação) - Curso de Engenharia de Controle e Automação, Universidade Federal do Rio de Janeiro, Rio de Janeiro, 2018.

MOUSER ELECTRONICS. Espressif Systems ESP32-WROOM-32 MCU Modules.
2018. | | | Disponível | | | | em:
https://br.mouser.com/new/espressif/espressif-esp32-wroom-32-modules/. | Acesso
em: 14 nov. 2022.

MY SOUS VIDE. My Sous Vide Home User. 2023. Disponível em: https://www.mysousvide.com.br/produto/mysousvidehomeuser/. Acesso em: 26 mar. 2023.

OLIVAN, Fernando. Menos de 40% das empresas nascidas no Brasil sobrevivem
após | cinco | anos, | diz | IBGE. | 2021. | Disponível | em:
https://fenacon.org.br/noticias/menos-de-40-das-empresas-nascidas-no-brasil-sobrevivem-apos-cinco-anos-diz-ibge/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,Segundo%20o%20I BGE%2C%20apenas%2037%2C6%25%20das%20empresas%20nascidas,e%20o% 20tamanho%20das%20empresas. Acesso em: 18 de dezembro de 2022.

ONEWIRE Driver. Disponível em: https://docs.pycom.io/tutorials/hardware/owd/. Acesso em: 11 abr. 2023.

OSTERWALDER, Alexander; PIGNEUR, Yves. Business Model Generation: inovação em modelos de negócios: um manual para visionários, inovadores e revolucionários. Rio de Janeiro - RJ: Alta Books, 2011. 293 p.

RAMOS, Ana E. A. O Sistema Sous Vide. 2004. 34 f. Monografia (Especialização) -Curso de Curso de Especialização Lato Sensu em Qualidade em Alimentos, Centro de Excelência em Turismo, Universidade de Brasília, Brasília, 2004.

RICARDO CUISINE. A Practical Guide to Sous-Vide Cooking. Disponível em: https://www.ricardocuisine.com/en/articles/special-feature/1167-a-practical-guide-to-s ous-vide-cooking. Acesso em: 14 nov. 2022.

SEBRAE - SERVIÇO BRASILEIRO DE APOIO ÀS MICRO E PEQUENAS EMPRESAS. Como elaborar um plano de negócios. Brasil. Brasília: Sebrae, 2013.

SEBRAE - SERVIÇO BRASILEIRO DE APOIO ÀS MICRO E PEQUENAS EMPRESAS. Sobrevivência das empresas no Brasil. Brasil. Brasília: Sebrae, 2016.

SILVA, Luana N. Controle PID de temperatura com integração de dados em rede. 2018. 65 f. TCC (Graduação) - Curso de Engenharia Mecatrônica, Departamento Acadêmico de Metal-Mecânica, Instituto Federal de Educação, Ciência e Tecnologia de Santa Catarina, Florianópolis, 2018.

SOCKET: Low-level networking interface. Low-level networking interface. 2023. Disponível em: https://docs.python.org/3/library/socket.html. Acesso em: 11 abr. 2023.

TEIXEIRA, Gustavo. Micropython ESP32: parte 1. Parte 1. 2019. Disponível em: https://www.usinainfo.com.br/blog/micropython-esp32-parte-1/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,microcontroladores%20e%20ambien tes%20com%20restri%C3%A7%C3%B5es. Acesso em: 17 mar. 2022.

THONNY: Python IDE for beginners. Python IDE for beginners. Disponível em: https://thonny.org/. Acesso em: 11 abr. 2023.

TIME: Time related functions. Time related functions. 2023. Disponível em: https://docs.micropython.org/en/latest/library/time.html. Acesso em: 11 abr. 2023.

ULU, | Tayfun. | WiFi | Manager. | 2023. | Disponível | em:
https://github.com/tayfunulu/WiFiManager. Acesso em: 11 abr. 2023.

VIANA, Flavia. A falta de planejamento é um dos vilões da mortalidade das
empresas | no | Brasil. | 2022. | Disponível | em:
https://sebraepr.com.br/comunidade/artigo/a-falta-de-planejamento-e-um-dos-viloes-da-mortalidade-das-empresas-no-brasil. Acesso em: 20 de dezembro de 2022.

ANEXO A - Direitos autorais - Lei nº 9.610, de 19 de fevereiro de 1998. Disposições preliminares
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

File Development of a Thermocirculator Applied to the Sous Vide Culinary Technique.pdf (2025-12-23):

1 BSc in Electrical Engineering.; Universidade; Estadual; Maringá.; BSc; Economics.; Universidade Cesumar. ORCID:; E-mail:; joaovmarcotti@hotmail.com.; 2 PhD in Chemical Engineering.; Maringá. ORCID: 0000-0003-2231- 9031. E-mail: camila.mir4@gmail.com.; MSc; Bioinformatics.; erinaldo.nascimento@unicesuma r.edu.br.

185

ARTIGO ORIGINAL

<< Recebido em 10/07/2025, Aceito em 21/11/2025 >>

10.18605/2175-7275/cereus.v17n4p185-196

Development of a Thermocirculator Applied to the Sous Vide Culinary Technique

ABSTRACT

This paper addresses the theory, design, and execution of a thermocirculator, developing its electronic circuits, printed circuit boards (PCBs), plastic structure, and equipment assembling. The developed thermocirculator is based on 3 previous prototypes, with the first one being created in 2019. The ESP32 microcontroller was used as the basis for the electronic circuits. MicroPython was chosen as the programming language, and a web server was developed to connect the user and the equipment via Wi-Fi, allowing monitoring of the equipment from anywhere. An On-Off controller was implemented to keep the water temperature constant. The plastic structure was made of ABS plastic, and manufactured by 3D printing, with lateral dimensions of 7 x 7 cm and 18.5 cm of height, divided into upper portion, medial cover, lower portion, and lower covers. The device has a manufacture cost around US$56 per unit, and a selling price estimated around US$140. After the equipment was assembled, tests were made to verify its operation, which consisted of preparing foods such as a NY strip steak at 55 ºC. In contrast to previous works, its design integrates a complete Wi-Fi monitoring system and ensures portability and compactness. The developed thermocirculator effectively maintained a stable water temperature and achieved cooking results comparable to commercial products, fulfilling the objectives established by this paper.

Keywords: 3D printing. ABS Plastic. Electronics. ESP32. MicroPython.

DOI: 10.18605/2175-7275/cereus.v17n4p185-196 Revista Cereus
2025 V. 17 N. 4

MARCOTTI JVP, MIRANDA CB, NASCIMENTO ES. Development of a Thermocirculator Applied to the Sous Vide Culinary Technique

186

### 1. INTRODUCTION

The term Sous Vide originates from French, translated into English as under vacuum

(Baldwin, 2012). The culinary technique itself involves cooking food that's vacuum-sealed in

a non-toxic plastic bag and placed in a container of water at a low and controlled temperature

(Borges, 2019). This culinary technique was first applied in 1970 by chef George Pralus at

the Troisgros restaurant, who was trying to develop a method to cook foie gras (translated

from French: duck liver) without altering the original texture of the food (Ramos, 2004).

The bag’s vacuum-sealing allows for more efficient heat transfer between water and

food and prevents the dilution of its flavors into the water (Borges, 2019). The original taste,

nutrients, and natural juices of the food are preserved using the Sous Vide technique,

resulting in a cooking quality impossible to achieve through traditional methods. Additionally,

this technique eliminates problems related to color, taste, and texture commonly associated

with frozen food. Furthermore, its application eradicates the risk of bacterial contamination

since during the cooking process, the food is fully pasteurized and isolated from the external

environment through vacuum-sealing (Ramos, 2004).

What captures the public and professional chefs’ attention regarding the use of the
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

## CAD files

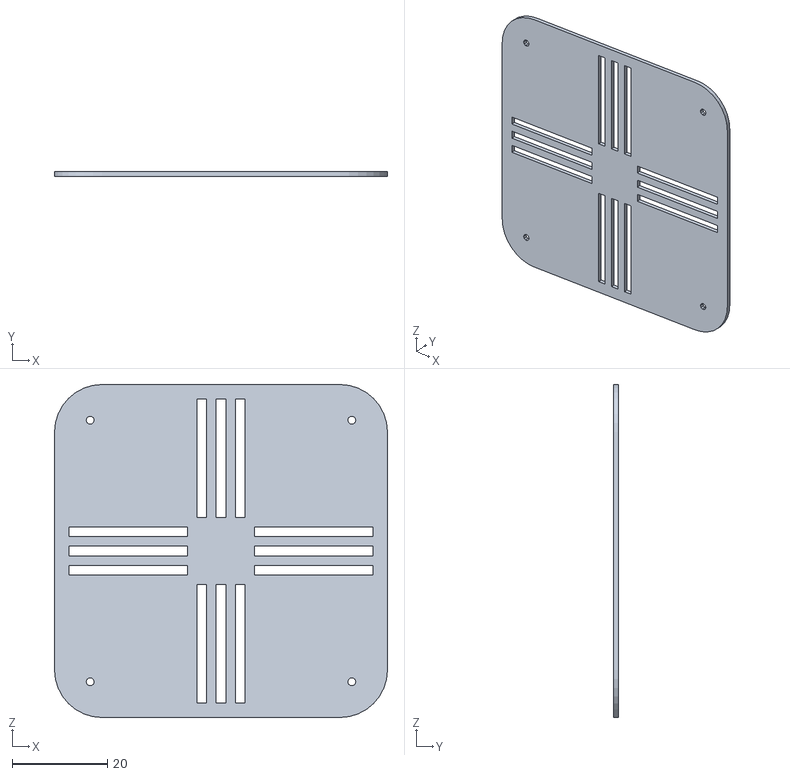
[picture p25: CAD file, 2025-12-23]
3D Printing Files/Tampa_Baixo_Definitivo_2.stl
70.0 x 1.00 x 70.0

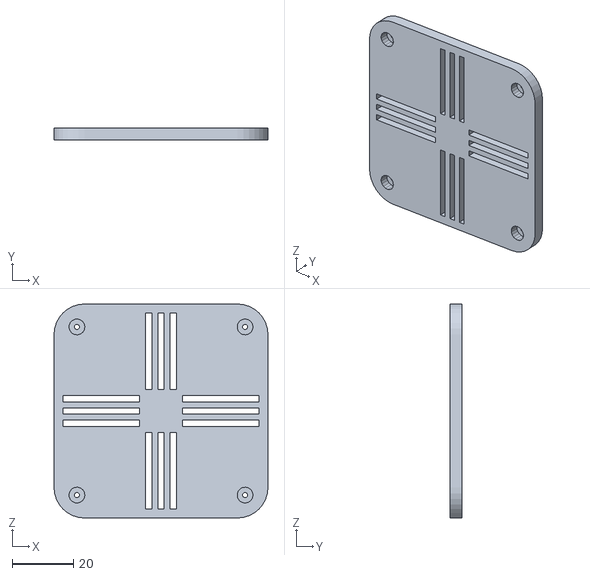
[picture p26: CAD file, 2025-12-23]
3D Printing Files/Tampa_Baixo_Definitivo_1.stl
70.0 x 4.00 x 70.0

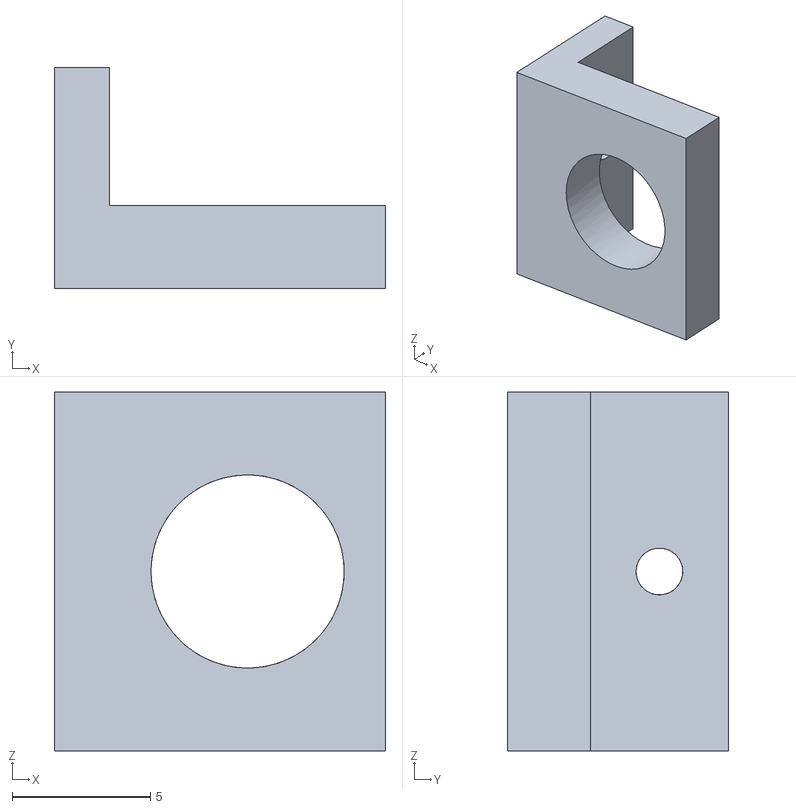
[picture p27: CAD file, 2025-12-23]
3D Printing Files/Suporte_Sonda.stl
12.0 x 8.00 x 13.0

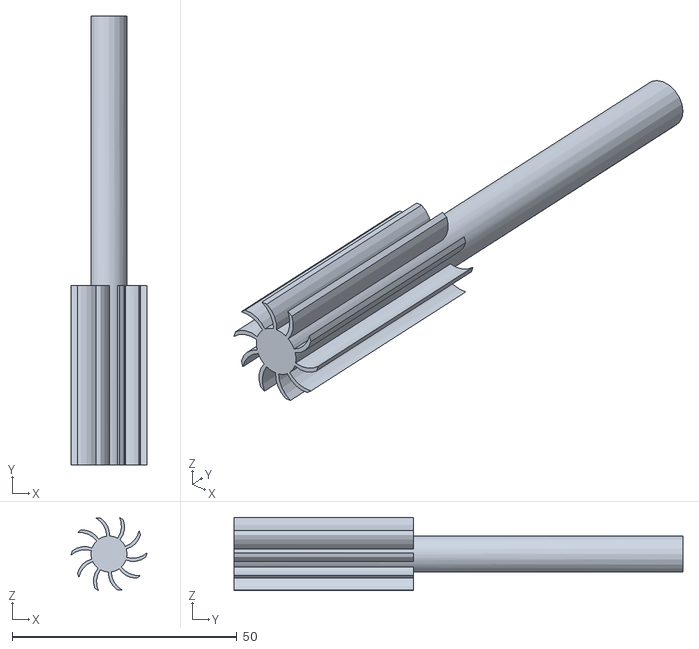
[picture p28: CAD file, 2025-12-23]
3D Printing Files/Helice_Definitivo.stl
17.0 x 100.0 x 16.3

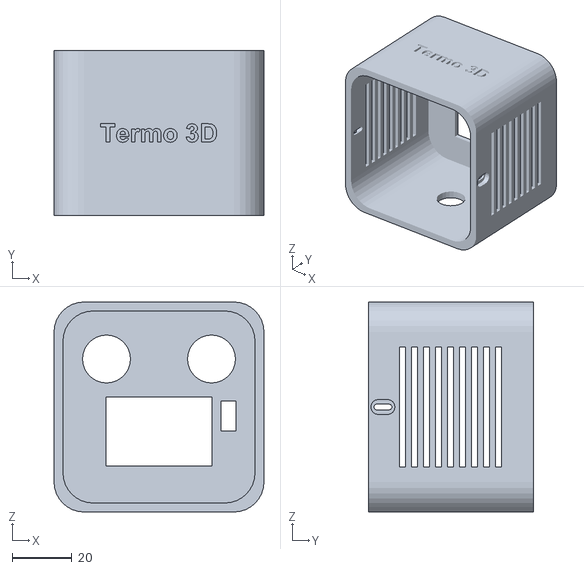
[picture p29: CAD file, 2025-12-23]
3D Printing Files/Cima_Definitivo.stl
70.0 x 55.0 x 70.0

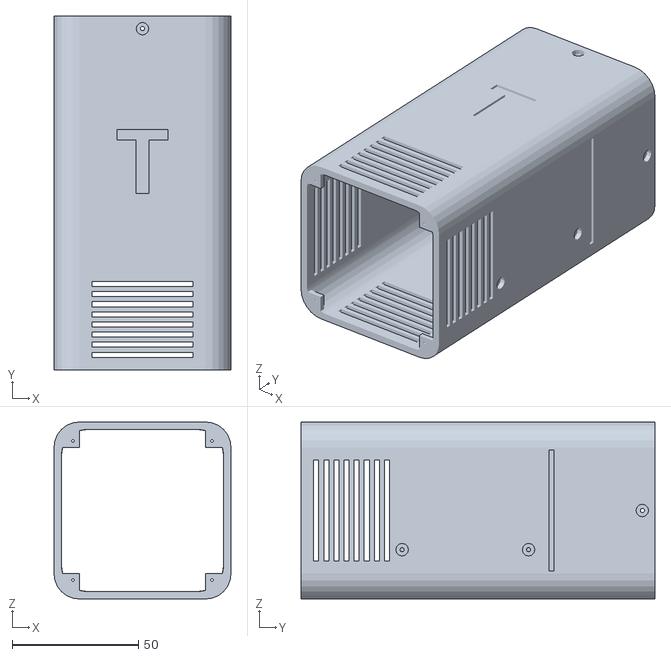
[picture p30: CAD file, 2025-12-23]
3D Printing Files/Baixo_Definitivo.stl
70.0 x 140.0 x 70.0

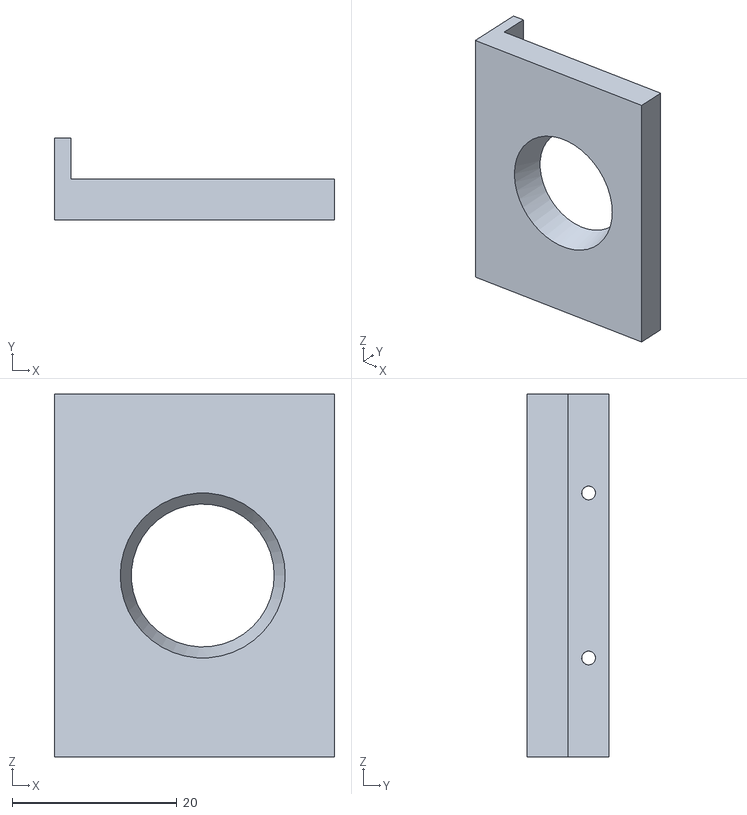
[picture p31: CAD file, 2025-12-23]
3D Printing Files/Suporte_Ebulidor.stl
34.0 x 10.0 x 44.0

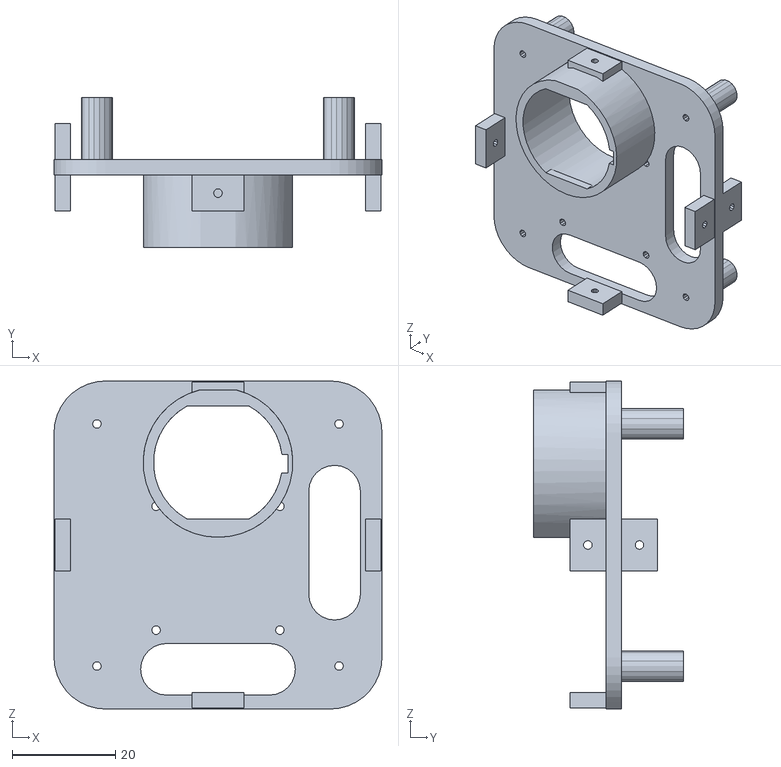
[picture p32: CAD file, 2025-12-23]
3D Printing Files/Medial_Definitivo.stl
63.6 x 29.0 x 63.6

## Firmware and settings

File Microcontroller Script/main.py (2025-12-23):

# Complete project details at https://RandomNerdTutorials.com
import network
import socket
import onewire, ds18x20, sh1106, time, os, sys, math
from machine import Pin, ADC, I2C
import machine
import wifimgr

# Defines the desired water temperature
desired_temp = 60

# Defines the values relateds to the thermistor
R1 = 950
Vs = 3.3
Beta = 3435
ADC_Res = 4095

# Defines the IO and ADC pins
plus_button = Pin(34, Pin.IN)
minus_button = Pin(18, Pin.IN, Pin.PULL_UP)
water_level = ADC(Pin(32, Pin.IN))
temp_sensor = ds18x20.DS18X20(onewire.OneWire((Pin(33))))
thermistor = ADC(Pin(35, Pin.IN))
ac_control = Pin(16, Pin.OUT)
cooler = Pin(25, Pin.OUT)
motor = Pin(26, Pin.OUT)
buzzer = Pin(4, Pin.OUT)

water_level.atten(ADC.ATTN_11DB)
thermistor.atten(ADC.ATTN_11DB)

# Scans the temperature sensor
roms = temp_sensor.scan()

# Defines the initial variable as 1, so it's necessary to press the 2 buttons to start the equipment
i=1

# Defines the display's I2C connection
i2c = I2C(scl=Pin(22), sda=Pin(21), freq=400000)
display = sh1106.SH1106_I2C(128, 64, i2c, None, 0x3c, rotate=180)
display.sleep(False)

wlan_sta = network.WLAN(network.STA_IF)
wlan = wifimgr.get_connection()
ip = wlan_sta.ifconfig()[0]
# Main Code goes here, wlan is a working network.WLAN(STA_IF) instance.
print("ESP OK")

def Internal_Temp():
    Rt = (R1*thermistor.read()/ADC_Res)/(1-(thermistor.read()/ADC_Res))
    Tc = -math.log(Rt/54921) / 0.072
    return Tc

def web_page_sleeping():
    
    html = """<html>
                <head>
                <title>Thermocirculator</title>
                <meta name="viewport" content="width=device-width, initial-scale=1">
                <link rel="icon" href="data:,">
                <link rel="stylesheet" href="https://cdnjs.cloudflare.com/ajax/libs/font-awesome/5.15.3/css/all.min.css">
                
                <meta http-equiv="refresh" content="1">
                
                <style>
                
                html
                {font-family: Arial;
                display:inline-block;
                margin: 0px auto;
                text-align: center;
                background-color: #191970}
                
                h1
                {color: #FFFFFF;
                padding: 2vh;
                font-size: 4em;}
                
                .button
                {display: inline-block;
                background-color: #FFFFFF;
                border: 2px solid #191970;
                border-radius: 8px;
                color: #191970;
                padding: 16px 40px;
                text-decoration: none;
                font-size: 30px;
                width: 210px;
                margin: 2px;
                cursor: pointer;
                -webkit-transition-duration: 0.4s; /* Safari */
                transition-duration: 0.4s;}
                
                .button:hover
                {background-color: #191970;
                color: #FFFFFF;
                border: 2px solid #FFFFFF;}
                
                </style>
                
                </head>
                
                <body>
                
                <br>
                
                <h1>Sleeping mode</h1>
                
                <p><i class="fas fa-bed" style="color:#FFFFFF; font-size: 4em;"></i></p>
                
                <br>
                
                </div>
                <div style="display: inline-block;">
                <a href="/?WakeUp_Button_Web=on"><button class="button">Wake up</button></a>
                </div>

                </body>
                </html>"""
    return html

def web_page_with_water():
    
    global Desired_Temp
    
    html = """<html>
                <head>
                <title>Thermocirculator</title>
                <meta name="viewport" content="width=device-width, initial-scale=1">
                <link rel="icon" href="data:,">
                <link rel="stylesheet" href="https://cdnjs.cloudflare.com/ajax/libs/font-awesome/5.15.3/css/all.min.css">
                
                <meta http-equiv="refresh" content="0.2">
                
                <style>
                
                html
                {font-family: Arial;
                display:inline-block;
                margin: 0px auto;
                text-align: center;}
                
                h1
                {color: #000000;
                padding: 2vh;
                font-size: 4em;
                text-align: center;}
                
                p
                {font-size: 2em;}
                
                .button_Sleep
                {display: inline-block;
                background-color: #000000;
                border: 2px solid #FFFFFF;
                border-radius: 8px;
                color: white;
                padding: 16px 40px;
                text-decoration: none;
                font-size: 30px;
                width: 210px;
                margin: 2px;
                cursor: pointer;
                -webkit-transition-duration: 0.4s; /* Safari */
                transition-duration: 0.4s;}
                
                .button_Sleep:hover
                {background-color: #FFFFFF; /* Green */
                color: #000000;
                border: 2px solid #000000;}
                
                </style>
                
                </head>
                
                <body>
                
                <br>
                
                <h1>Thermocirculator Web Server</h1>
                
                <br>
                
                <p><i class="fas fa-thermometer-half"></i>  Thermocirculator internal temperature: <strong>""" + str(round(Intern_Temp,1)) + """ *C</strong></p>
                
                <p><i class="fas fa-fan"></i>  Cooler status: <strong>""" + cooler_State + """</strong></p>
                
                <br>
                
                <p><i class="fas fa-thermometer-half"></i>  Current Water temperature: <strong>""" + str(round(water_temp,1)) + """ *C</strong></p>
                
                <br>
                
                <p><i class="fas fa-thermometer-half"></i>  Desired Water temperature: <strong>""" + str(round(desired_temp,1)) + """ *C</strong></p>
                
                <br>
                <br>
                
                </div>
                <div style="display: inline-block;">
                <a href="/?Sleep_Button_Web=on"><button class="button_Sleep">Sleep</button></a>
                </div>
                
                </body>
                </html>"""
    return html

def web_page_no_water():
    
    html = """<html>
                <head>
                <title>Thermocirculator</title>
                <meta name="viewport" content="width=device-width, initial-scale=1">
                <link rel="icon" href="data:,">
                <link rel="stylesheet" href="https://cdnjs.cloudflare.com/ajax/libs/font-awesome/5.15.3/css/all.min.css">
                
                <meta http-equiv="refresh" content="1">
                
                <style>
                
                html
                {font-family: Arial;
                display:inline-block;
                margin: 0px auto;
                background-color: #FA8072;
                text-align: center;}
                
                h1
                {color: #000000;
                padding: 2vh;
                font-size: 4em;}
                
                p
                {font-size: 2em;}
                
                .button_Sleep
                {display: inline-block;
                background-color: #000000;
                border: 2px solid #FA8072;
                border-radius: 8px;
                color: #FA8072;
                padding: 16px 40px;
                text-decoration: none;
                font-size: 30px;
                width: 210px;
                margin: 2px;
                cursor: pointer;
                -webkit-transition-duration: 0.4s; /* Safari */
                transition-duration: 0.4s;}
                
                .button_Sleep:hover
                {background-color: #FA8072; /* Green */
                color: #000000;
                border: 2px solid #000000;}
                
                </style>
                
                </head>
                
                <body>
                
                <br>
                
                <h1>DANGER!!</h1>
                
                <i class="fas fa-exclamation-triangle" style="color:#000000; font-size: 4em;"></i>
                
                <br>
                
                <p>No water level detected.</strong></p>

                <br>

                </div>
                <div style="display: inline-block;">
                <a href="/?Sleep_Button_Web=on"><button class="button_Sleep">Sleep</button></a>
                </div>

                </body>
                </html>"""
    return html

try:
  s = socket.socket(socket.AF_INET, socket.SOCK_STREAM)
  s.setsockopt(socket.SOL_SOCKET, socket.SO_REUSEADDR, 1)
  s.bind(('', 80))
  s.listen(5)
  s.setblocking(False)
except OSError as e:
  machine.reset()

while True:
    
    # if the initial variable is equal to 0 the equipment will be started
    if (i==0):

        if (j==0):
            # Defines the welcome message to be showed by the equipment
            # Cleans the display
            display.fill(0)
            # Text to be showed by the display
            display.text('Termo 3D', 28, 30, 1)
            display.show()
            # Keeps the text in the display during 5 seconds
            time.sleep(4)
        
        j=1
        
        # If the water level sensor detects water
        if (water_level.read() > 1000):
            
            # Turns off the buzzer
            buzzer.value(0)
            # Turns on the motor
            motor.value(1)
            # Calculates the internal temperature measured by the thermistor
            internal_temp = Internal_Temp()
            
            # Gets the water temperature measured by the sensor
            temp_sensor.convert_temp()
            time.sleep_ms(1000)
            for rom in roms:
                water_temp = temp_sensor.read_temp(rom)
            
            # Cleans the display
            display.fill(0)
            # Shows the water temperature
            display.text('Temperatura', 0, 10, 1)
            display.text('Atual:', 0, 25, 1)
            display.text(str(round(water_temp,1)), 0, 45, 1)
            display.text('C', 35, 45, 1)
            display.show()
            time.sleep_ms(10)
            
            # If the plus button is pressed, decrease the desired temperature by 1
            if (plus_button.value()==0 and minus_button.value()==1):
                desired_temp -= 0.5
                display.fill(0)
                display.text('Temperatura', 0, 10, 1)
                display.text('Desejada:', 0, 25, 1)
                display.text(str(round(desired_temp,2)), 0, 45, 1)
                display.text('C', 35, 45, 1)
                display.show()
                time.sleep(0.5)
            
            # If the minus button is pressed, increase the desired temperature by 1
            if (minus_button.value()==0 and plus_button.value()==1):
                desired_temp += 0.5
                display.fill(0)
                display.text('Temperatura', 0, 10, 1)
                display.text('Desejada:', 0, 25, 1)
                display.text(str(round(desired_temp,1)), 0, 45, 1)
                display.text('C', 35, 45, 1)
                display.show()
                time.sleep(0.5)
            
            # If the internal temperature is greater than 30ºC turns on the cooler
            if (internal_temp > 30):
                cooler.value(1)
            else:
                cooler.value(0)
            
            if cooler.value() == 1:
                cooler_State = "ON"
            else:
                cooler_State = "OFF"
                
            Intern_Temp = Internal_Temp()
            
            # If the water temperature is lower than the desired temperature turns on the heater
            if (water_temp<desired_temp):
                ac_control.value(1)

            if (water_temp>=desired_temp):
                ac_control.value(0)
            
            print(water_temp<desired_temp)
            
            # If the two buttons are pressed when the equipment is working, turns it off by setting the initial variable as 1
            if (plus_button.value()==0 and minus_button.value()==0):
                i=1
                # Turns off the buzzer
                buzzer.value(0)
                motor.value(0)
                cooler.value(0)
                # Shows a sleepy face when the equipment isn't working
                display.fill(0)
                display.text('--      --', 23, 10, 1)
                display.text('------', 40, 50, 1)
                display.show()
                time.sleep(2)
                
                if gc.mem_free() < 102000:
                    gc.collect()
                try:
                    conn, addr = s.accept()
                except OSError as e:
                    if e.args[0] == errno.EAGAIN or e.args[0] == errno.EWOULDBLOCK:
                        # não há novas conexões pendentes, continue o loop
                        continue
                    raise
                conn.settimeout(20.0)
                print('Got a connection from %s' % str(addr))
                request = conn.recv(1024)
                conn.settimeout(None)
                request = str(request)
                print('Content = %s' % request)
                
                response = web_page_no_water()
                conn.send('HTTP/1.1 200 OK\n')
                conn.send('Content-Type: text/html\n')
                conn.send('Connection: close\n\n')
                conn.sendall(response)
                conn.close()

            if gc.mem_free() < 102000:
                gc.collect()
            try:
                conn, addr = s.accept()
            except OSError as e:
                if e.args[0] == errno.EAGAIN or e.args[0] == errno.EWOULDBLOCK:
                    # não há novas conexões pendentes, continue o loop
                    continue
                raise
            conn.settimeout(20.0)
            print('Got a connection from %s' % str(addr))
            request = conn.recv(1024)
            conn.settimeout(None)
            request = str(request)
            print('Content = %s' % request)
            response = web_page_with_water()
            conn.send('HTTP/1.1 200 OK\n')
            conn.send('Content-Type: text/html\n')
            conn.send('Connection: close\n\n')
            conn.sendall(response)
            conn.close()

            Sleep_Button_Web = request.find('/?Sleep_Button_Web=on')

            # If the two buttons are pressed when the equipment is working, turns it off by setting the initial variable as 1
            if (Sleep_Button_Web==6):
                i=1
                # Turns off the buzzer
                buzzer.value(0)
                motor.value(0)
                cooler.value(0)
                ac_control.value(0)
                
                # Shows a sleepy face when the equipment isn't working
                display.fill(0)
                display.text('--      --', 23, 10, 1)
                display.text('------', 40, 50, 1)
                display.show()
                time.sleep(2)
                
                if gc.mem_free() < 102000:
                    gc.collect()
                try:
                    conn, addr = s.accept()
                except OSError as e:
                    if e.args[0] == errno.EAGAIN or e.args[0] == errno.EWOULDBLOCK:
                        # não há novas conexões pendentes, continue o loop
                        continue
                    raise
                conn.settimeout(20.0)
                print('Got a connection from %s' % str(addr))
                request = conn.recv(1024)
                conn.settimeout(None)
                request = str(request)
                print('Content = %s' % request)
                
                response = web_page_no_water()
                conn.send('HTTP/1.1 200 OK\n')
                conn.send('Content-Type: text/html\n')
                conn.send('Connection: close\n\n')
                conn.sendall(response)
                conn.close()

            Plus_Button_Web = request.find('/?Plus_Button_Web=on')
            Minus_Button_Web = request.find('/?Minus_Button_Web=on')
            
            if Plus_Button_Web == 6:
                desired_temp += 0.5
            if Minus_Button_Web == 6:
                desired_temp -= 0.5
        
        # If the water level sensor doesn't detect water
        else:
            
            # Turns on the buzzer as a warning
            buzzer.value(1)
            # Turns off the heater 
            ac_control.value(0)
            # Turns off the motor
            motor.value(0)
            # Clens the display
            display.fill(0)
            # Advise that there is no water
            display.text('WARNING', 34, 15, 1)
            display.text('NO WATER', 30, 30, 1)
            display.text('DETECTED', 30, 45, 1)
            display.show()
            
            # If the two buttons are pressed when the equipment is working, turns it off by setting the initial variable as 1
            if (plus_button.value()==0 and minus_button.value()==0):
                i=1
                # Turns off the buzzer
                buzzer.value(0)
                motor.value(0)
                cooler.value(0)
                ac_control.value(0)
                
                # Shows a sleepy face when the equipment isn't working
                display.fill(0)
                display.text('--      --', 23, 10, 1)
                display.text('------', 40, 50, 1)
                display.show()
                time.sleep(2)
        
                if gc.mem_free() < 102000:
                    gc.collect()
                try:
                    conn, addr = s.accept()
                except OSError as e:
                    if e.args[0] == errno.EAGAIN or e.args[0] == errno.EWOULDBLOCK:
                        # não há novas conexões pendentes, continue o loop
                        continue
                    raise
                conn.settimeout(20.0)
                print('Got a connection from %s' % str(addr))
                request = conn.recv(1024)
                conn.settimeout(None)
                request = str(request)
                print('Content = %s' % request)
                
                response = web_page_no_water()
                conn.send('HTTP/1.1 200 OK\n')
                conn.send('Content-Type: text/html\n')
                conn.send('Connection: close\n\n')
                conn.sendall(response)
                conn.close()
            
            if gc.mem_free() < 102000:
                gc.collect()
            try:
                conn, addr = s.accept()
            except OSError as e:
                if e.args[0] == errno.EAGAIN or e.args[0] == errno.EWOULDBLOCK:
                    # não há novas conexões pendentes, continue o loop
                    continue
                raise
            print('1')
            conn.settimeout(20.0)
            print('Got a connection from %s' % str(addr))
            request = conn.recv(1024)
            conn.settimeout(None)
            request = str(request)
            print('Content = %s' % request)
            
            response = web_page_no_water()
            conn.send('HTTP/1.1 200 OK\n')
            conn.send('Content-Type: text/html\n')
            conn.send('Connection: close\n\n')
            conn.sendall(response)
            conn.close()
            
            Sleep_Button_Web = request.find('/?Sleep_Button_Web=on')
            
            # If the two buttons are pressed when the equipment is working, turns it off by setting the initial variable as 1
            if (Sleep_Button_Web==6):
                i=1
                # Turns off the buzzer
                buzzer.value(0)
                motor.value(0)
                cooler.value(0)
                ac_control.value(0)
                
                # Shows a sleepy face when the equipment isn't working
                display.fill(0)
                display.text('--      --', 23, 3, 1)
                display.text('------', 40, 27, 1)
                display.text('IP: ', 3, 55, 1)
                display.text(ip, 28, 55, 1)
                display.show()
                time.sleep(2)
        
                if gc.mem_free() < 102000:
                    gc.collect()
                try:
                    conn, addr = s.accept()
                except OSError as e:
                    if e.args[0] == errno.EAGAIN or e.args[0] == errno.EWOULDBLOCK:
                        # não há novas conexões pendentes, continue o loop
                        continue
                    raise
                conn.settimeout(20.0)
                print('Got a connection from %s' % str(addr))
                request = conn.recv(1024)
                conn.settimeout(None)
                request = str(request)
                print('Content = %s' % request)
                
                response = web_page_no_water()
                conn.send('HTTP/1.1 200 OK\n')
                conn.send('Content-Type: text/html\n')
                conn.send('Connection: close\n\n')
                conn.sendall(response)
                conn.close()
            
    else:
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
